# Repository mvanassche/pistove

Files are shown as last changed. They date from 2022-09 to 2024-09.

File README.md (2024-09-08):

Raspberry pi

```
sudo apt-get install openjdk-11-jdk
```
```
sudo apt-get install pigpio
```

# Hardware

## Stove

- [Manual air valve register](https://www.jpvos.be/nl/dixneuf-warmeluchtroosters-toe-afvoer/9882-register-met-kabel-diam160-met-messing-knop.html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)
- [Belimo LM230A](https://www.ventilatieland.be/fr_BE/p/belimo-servomotor-230v-o-d-5-nm-lm230a-tp/8749/) note: you can probably go with a much smaller and cheaper model
- [Air valve register](https://www.ventilatieland.be/nl_BE/p/motorbediende-regelklep-o-160mm-voor-spirobuis/8945/)

## Raspberry Pi

There are 2 versions, a cheaper version with limited display, and a more expensive with a touch screen. For both versions, a web page exposes a user interface (the same as the touch screen).  

- [ceramic oven probe, k type thermocouple](https://www.amazon.com.be/ceramic-mounting-thermocouple-sensor-temperature/dp/B09XX7Y9TY) for the hot fumes
- [MAX31855 - V2.0](https://shop.mchobby.be/fr/temperature/302-amplificateur-thermocouple-max31855-v20-3232100003026-adafruit.html)
- [Thermocouple Type-K](https://shop.mchobby.be/fr/temperature/301-thermocouple-type-k-3232100003019.html) for the cold fumes and the accumulator t°
- [SHT31-F](https://shop.mchobby.be/fr/environnemental-press-temp-hrel-gaz/1882-sht31-f-capteur-d-humidite-et-temperature-3232100018822-dfrobot.html) for indoor t°
- [Piezo buzzer](https://shop.mchobby.be/fr/autres-capteurs/57-piezo-buzzer-3232100000575.html)
- [DS18B20](https://shop.mchobby.be/fr/environnemental-press-temp-hrel-gaz/151-capteur-temperature-ds18b20-etanche-extra-3232100001510.html) for outside t°
- [Relay 5v | 2-canals](https://www.bol.com/be/nl/p/otronic-relais-module-5v-2-kanaals-arduino-esp32-esp8266-raspberry-pi-wemos/9300000011396590/) to control the register

### Version pi zero 2 W

- [Raspberry Pi Zero 2 with HEADER](https://shop.mchobby.be/fr/pi-zero-12wwh/2334-raspberry-pi-zero-2-w-avec-header-wireless-cam-port-3232100023345.html)
- [LCD 16x2 I2C](https://shop.mchobby.be/fr/afficheur-lcd-tft-oled/1807-afficheur-lcd-16x2-i2c-3232100018075-dfrobot.html)
- push buttons

### Version pi 4B

- Raspberry 4B 1G
- [4.3inch HDMI LCD (B) - 800x480 - IPS - Capacitive touch](https://www.kiwi-electronics.com/nl/4-3inch-hdmi-lcd-b-800x480-ips-capacitive-touch-4065)
- Rotary button

### Pi wiring

# Software

## Pi

`sudo nano /etc/xdg/lxsession/LXDE-pi/autostart`

```
@lxpanel --profile LXDE-pi
@pcmanfm --desktop --profile LXDE-pi
@xscreensaver -no-splash
@/etc/xdg/lxsession/LXDE-pi/stove-kiosk.sh
```

`sudo nano /etc/rc.local`

```
(cd /home/pi/stove/ && sudo java -jar pistove-2.0-SNAPSHOT-all.jar)
```

`sudo nano /etc/xdg/lxsession/LXDE-pi/stove-kiosk.sh`

```
  GNU nano 5.4                                                         /etc/xdg/lxsession/LXDE-pi/stove-kiosk.sh
#!/bin/bash

(sleep 20 && chromium-browser --kiosk http://localhost:8080/)

```

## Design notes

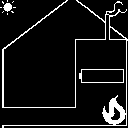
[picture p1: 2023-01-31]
src/commonMain/resources/background-oled.bmp

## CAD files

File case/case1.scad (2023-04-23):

width = 135;
height = 180;
depth = 50;

wallThickness = 2;



difference() {
    cube([height, width, depth - wallThickness]);
        // general box
    translate([-1, wallThickness, wallThickness])
        cube([height - wallThickness + 1, width - (2 * wallThickness) , depth + 1]);
        // bottom hole
    translate([30, 20, -1])
        cube([45, 80, wallThickness * 2]);
        // cable hole
    translate([150, 109 - 5, 0]) rotate([90, 0, 90])
        cylinder(h = height, r = 5);
    translate([40, 100 - 5, -1])
        cube([120, 5, 15]);

        // cover ridge
    translate([2, 2, height - 2])
        cube([height - 4, width - 4, 5]);
        // side buttons hole
    translate([16, -1, depth - 16])
        cube([54, 10, 8]);
    
        // ventilation bottom
    for (i = [0 : (width / 7)]){
        translate([height - wallThickness - 1, 10 + (i * 6), 10])
            cube([5, 3, depth - 20]);
    }    

    // hole for auto button
    translate([height - 15, 109 - 5, 33]) rotate([0, 90, 90])
        cylinder(h = height, r = 8);

    // hole for rotary button
    translate([height - 15, 109 - 5, 13]) rotate([0, 90, 90])
        cylinder(h = height, r = 4);
    
}

    // support max's
/*translate([height - 80 - 40, width - 10 - wallThickness, 22])
    cube([80, 11, wallThickness]);*/
translate([height - 80 - 40, width - 4, 0])
    cylinder(22, r = 2.5);



// cover
color("blue")
//translate([0, width + 20, 0])
rotate([180, 0, 0]) translate([0, 10, -depth])
difference() {
    cube([height + wallThickness, width, depth]);
    translate([wallThickness, -1, -1])
        cube([height + 10, width + 2, depth - wallThickness + 1]);
    
    // screen hole
    translate([14, 8, depth - wallThickness - 1])
        cube([59, 98, wallThickness * 2]);
    
        // ventilation top
    for (i = [0 : (width / 7)]){
        translate([-1, 10 + (i * 6), 10])
            cube([5, 3, depth - 20]);
    }

}

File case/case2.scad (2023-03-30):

width = 112;
height = 200;
depth = 50;

wallThickness = 2;
maxWidth = 21; // MAX81355



difference() {
    cube([height, width, depth - wallThickness]);
        // general box
    translate([-1, wallThickness, wallThickness])
        cube([height - wallThickness + 1, width - (2 * wallThickness) , depth + 1]);
    
        // bottom hole
    translate([20, 20, -1])
        cube([50, 70, wallThickness * 2]);
    
    translate([height - 50, 75, -1])
        cube([40, 16, wallThickness * 2]);
    
        // cable hole
    translate([height - 25, 20 - 5, 0]) rotate([90, 0, 0])
        cylinder(h = height, r = 5);
    translate([height - 55, 10, -1])
        cube([46, 21, 15]);

        // cover ridge
    translate([2, 2, height - 2])
        cube([height - 4, width - 4, 5]);
    
        // side buttons hole
    translate([16, -1, depth - 16])
        cube([54, 10, 8]);
    
        // ventilation bottom
    margin = 10;
    for (i = [0 : ((width - 2*margin) / 6)]){
        translate([height - wallThickness - 1, margin + (i * 6), 10])
            cube([5, 3, depth - 20]);
    }    

    // hole for auto button
    translate([height - 15, 109 - 5, 33]) rotate([0, 90, 90])
        cylinder(h = height, r = 8);

    // hole for rotary button
    translate([height - 15, 109 - 5, 13]) rotate([0, 90, 90])
        cylinder(h = height, r = 4);

    // support screen
    translate([14, (width - 99) / 2, -1]) {
        translate([0, 0, 0])
            cylinder(10, r = 1.5);
        
        translate([0, 99, 0])
            cylinder(10, r = 1.5);

        translate([60, 99, 0])
            cylinder(10, r = 1.5);

        translate([60, 0, 0])
            cylinder(10, r = 1.5);
    }
    
    // holes for screws wall
    translate([40, 10, -1])
        cylinder(10, r = 4);
    translate([36, 10, -1])
        cylinder(10, r = 2);
    translate([35, 10, -1])
        cylinder(10, r = 2);

    translate([40, width - 10, -1])
        cylinder(10, r = 4);
    translate([36, width - 10, -1])
        cylinder(10, r = 2);
    translate([35, width - 10, -1])
        cylinder(10, r = 2);
    
    // holes for max's

    for (i = [1 : 3]) {
        translate([height - (maxWidth * i)  - 50 + 7.8, width - 4, 8.5]) rotate([0, 90, 90])
            cylinder(5, r = 3.5);
    }
}

    // support max's
for (i = [1 : 3]) {
    translate([height - (maxWidth * i)  - 50, width - 4, 0])
        cylinder(5, r = 2.5);

    translate([height - (maxWidth * i) + 15  - 50, width - 4, 0])
        cylinder(5, r = 2.5);
}

    // support dispatcher
translate([14 + 60 + 10, 0, 0])
    cube([55, wallThickness + 5, wallThickness + 2]);
translate([14 + 60 + 10, wallThickness + 78 - 5, 0])
    cube([55, 5, wallThickness + 2]);


    // support screen
difference() {
    translate([14, (width - 99) / 2, 0]) {
        translate([0, 0, 0])
            cylinder(10, r = 4);
        
        translate([0, 99, 0])
            cylinder(10, r = 4);

        translate([60, 99, 0])
            cylinder(10, r = 4);

        translate([60, 0, 0])
            cylinder(10, r = 4);
    }

    translate([14, (width - 99) / 2, -1]) {
        translate([0, 0, 0])
            cylinder(10, r = 3);
        
        translate([0, 99, 0])
            cylinder(10, r = 3);

        translate([60, 99, 0])
            cylinder(10, r = 3);

        translate([60, 0, 0])
            cylinder(10, r = 3);
    }
    
}

// cover
color("blue")
    //translate([0, width + 20, 0])
    //translate([-2.2, 0 , 0])
    rotate([180, 0, 0]) translate([0, 10, -depth]) {
    difference() {
        translate([0, -0.2, 0]) cube([height + wallThickness + 1.5, width + 0.4, depth]);
        translate([wallThickness, -1, -1])
            cube([height + 10, width + 2, depth - wallThickness + 1]);
        
        // screen hole
        screenHoleWidth = 98;
        translate([14, (width - screenHoleWidth - 2*wallThickness)/2 + wallThickness, depth - wallThickness - 1])
            cube([59, screenHoleWidth, wallThickness * 2]);
        
            // ventilation top
        margin = 10;
        for (i = [0 : ((width - 2*margin) / 6)]){
            translate([-1, margin + (i * 6), 10])
                cube([5, 3, depth - 20]);
        }
        
        
    }
    // pattes
    /*translate([0, wallThickness + 0.4, depth - 5])
        cube([5, wallThickness, 5]);

    translate([0, width - wallThickness - wallThickness - 0.4, depth - 5])
        cube([5, wallThickness, 5]);*/

    /*translate([0, wallThickness + 0.5, wallThickness + 0.5])
        cube([5, wallThickness, 5]);

    translate([0, width - wallThickness - wallThickness - 0.5, wallThickness + 0.5])
        cube([5, wallThickness, 5]);*/

    translate([height - 10, wallThickness + 0.4, depth - 5])
        cube([5, wallThickness, 5]);

    translate([height - 10, width - wallThickness - wallThickness - 0.4, depth - 5])
        cube([5, wallThickness, 5]);
    
    // border
    translate([0, -wallThickness - 0.1, depth - 7])
        cube([height + wallThickness + 1.5, wallThickness, 7]);

    translate([0, -wallThickness - 0.1, 0])
        cube([15, wallThickness, depth]);


    translate([0, width + 0.1, depth - 7])
        cube([height + wallThickness + 1.5, wallThickness, 7]);
    translate([0, width + 0.1, 0])
        cube([15, wallThickness, depth]);
    
}

// stuff DO NOT PRINT
color("red") {

}

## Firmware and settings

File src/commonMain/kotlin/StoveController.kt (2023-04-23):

import kotlinx.coroutines.awaitCancellation
import kotlinx.coroutines.coroutineScope
import kotlinx.coroutines.flow.StateFlow
import kotlinx.coroutines.flow.map
import kotlinx.coroutines.flow.stateIn
import kotlinx.coroutines.launch
import kotlinx.datetime.Instant
import kotlinx.serialization.Serializable
import kotlinx.serialization.Transient
import pistove.status.physical.Environment
import kotlin.math.max
import kotlin.time.Duration.Companion.minutes
import kotlin.time.Duration.Companion.seconds


fun stoveController(): StoveController {
    val powerRelay = LowActiveGPIOElectricRelay("power-relay", 5)
    val openCloseRelay = LowActiveGPIOElectricRelay( "direction-relay", 6)
    val valve = ElectricValveController("air-intake-valve", powerRelay = powerRelay, openCloseRelay = openCloseRelay)
    //val fumes = TestTemperatureSensor("stove-thermometer").also { it.usefulPrecision = 0 }
    val fumes = MAX31855TemperaturSensor("stove-thermometer", 0, 0).also { it.usefulPrecision = 0 }
    //val accumulator = EmptyTemperatureSensor("accumulator-thermometer")
    val accumulator = MAX31855TemperaturSensor("accumulator-thermometer", 0, 1).also { it.usefulPrecision = 0 }
    val room = SHT31TemperaturSensor("room-thermometer", 1, 0x45).also { it.usefulPrecision = 1 }
    val outsideTemperatureSensor = DS18B20TempartureSensor("outside-thermometer", 0x1b9c071e64ff.toULong()).also { it.usefulPrecision = 0 }
    val buzzer = PassivePiezoBuzzerHardwarePWM("buzzer", 12)
    val openButton = PushButtonGPIO("open-button", 13, DigitalState.high)
    val closeButton = PushButtonGPIO("close-button", 26, DigitalState.high)
    val rechargeButton = PushButtonGPIO("recharge-button", 19, DigitalState.high)
    val display = Display1602LCDI2C("display", 1, 0x27)
    val comm = DisplayAndBuzzerUserCommunication("user-communication", display, buzzer)
    return StoveController("stove", valve, fumes, accumulator, room, outsideTemperatureSensor, openButton, closeButton, rechargeButton, comm)
}

@Serializable
class StoveController(
    override val id: String,
    val valve: ElectricValveController,
    val fumes: TemperatureSensor,
    val accumulator: TemperatureSensor,
    val room: TemperatureSensor,
    val outside: TemperatureSensor,
    val openButton: PushButton,
    val closeButton: PushButton,
    val rechargeButton: PushButton,
    val userCommunication: BasicUserCommunication
) : Controller {

    val accumulatorLowTemperature = 30.0
    val accumulatorHighTemperature = 130.0

    @Transient
    val lastUserValveRate = PersistentStateWithTimestamp<Double?>(null)

    @Transient
    val lastTimeRecharged = PersistentStateWithTimestamp<Unit>(Unit)

    @Transient
    var daFumes: StateFlow<InstantValue<Double>>? = null

    @Transient
    var chargedRate: StateFlow<InstantValue<Double>>? = null

    @Transient
    var autoModeController: AutoModeController? = null

    override suspend fun startControlling(): Boolean {
        // ??? what to do? should we start all here or assume they are started elsewhere?
        coroutineScope {

            val fumesSmoothed = fumes.windowed(30.0.seconds)
                .aggregate { it.average() }
                .sampleInstantValue(30.0.seconds)

            // average fumes before  deriving for less noise?
            val dFumes = fumesSmoothed.zipWithNext().map {
                if (it.second.time > it.first.time) {
                    InstantValue(
                        (it.second.value - it.first.value) / ((it.second.time.toEpochMilliseconds() - it.first.time.toEpochMilliseconds()).toDouble() / 3600000.0), // in °/h
                        Instant.fromEpochMilliseconds((it.first.time.toEpochMilliseconds() + it.second.time.toEpochMilliseconds()) / 2)
                    )
                } else {
                    InstantValue(0.0, it.second.time)
                }
            }

            launch { valve.startControlling() }
            launch { fumes.startSensing() }
            launch { accumulator.startSensing() }
            launch { room.startSensing() }
            launch { outside.startSensing() }
            launch { openButton.startSensing() }
            launch { closeButton.startSensing() }
            launch { rechargeButton.startSensing() }
            openButton.addOnClickListener { this.launch { openSome() } }
            closeButton.addOnClickListener { this.launch { closeSome() } }
            openButton.addOnLongClickListener { this.launch { open() } }
            closeButton.addOnLongClickListener { this.launch { close() } }
            rechargeButton.addOnClickListener { this.launch { onRecharged() } }
            identifieables.filterIsInstance<WatcheableState>().forEach {
                it.addOnStateChange { launch { refreshDisplay() } }
            }
            launch {
                daFumes = dFumes.windowed(5.0.minutes).map {
                    InstantValue(it.map { it.value }.average(), it.last().time)
                }.stateIn(this)
                autoModeController = SlowlyCloseWhenCooling("auto-close", valve, fumes, daFumes!!, lastUserValveRate, lastTimeRecharged)
                autoModeController?.startControlling()
            }
            launch {
                chargedRate = accumulator.windowed(5.0.minutes).map {
                    InstantValue((max(0.0, it.map { it.value }.average() - accumulatorLowTemperature) / (accumulatorHighTemperature - accumulatorLowTemperature)))
                }.stateIn(this)
            }
            awaitCancellation()
        }
        return true
    }

    override val devices: Set<Device>
        get() = setOf(fumes, accumulator, room, outside, openButton, closeButton, rechargeButton) + valve.devices + userCommunication.devices

    override val identifieables: Set<Identifiable>
        get() = devices + valve + (autoModeController?.let { setOf(it) } ?: emptySet())

    fun stopControlling() {

    }

    suspend fun setOpenRateTo(rate: Double) {
        userCommunication.acknowledge()
        lastUserValveRate.state = rate
        if(valve.setOpenRateTo(rate)) {
            userCommunication.acknowledge()
        }
    }
    suspend fun open() {
        setOpenRateTo(1.0)
    }
    suspend fun openSome() {
        setOpenRateTo((valve.openRateOrTarget ?: 0.0) + 0.1)
    }
    suspend fun closeSome() {
        setOpenRateTo((valve.openRateOrTarget ?: 1.0) - 0.1)
    }
    suspend fun close() {
        setOpenRateTo(0.0)
    }

    suspend fun auto() {
        userCommunication.acknowledge()
        autoModeController?.let { it.enabled = !it.enabled }
    }

    suspend fun onRecharged() {
        lastTimeRecharged.state = Unit
        userCommunication.acknowledge()
    }

    suspend fun refreshDisplay() {
        (userCommunication as? StringDisplay)?.displayTable(stateDisplayString())
    }
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

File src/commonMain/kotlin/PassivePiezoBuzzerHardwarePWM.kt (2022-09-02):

import kotlinx.coroutines.delay
import kotlinx.serialization.Serializable
import kotlinx.serialization.Transient
import kotlin.time.Duration

@Serializable
class PassivePiezoBuzzerHardwarePWM(override val id: String, val bcm: Int, val hardware: Boolean = (bcm in listOf(12, 13, 18, 19))) : Buzzer, TestableDevice {

    @Transient
    val pwm: GPIOPWM = pi.pwm(bcm, hardware).also {
        it.dutyCycle = 50.0
    }

    override suspend fun beep(duration: Duration) {
        beep(4000, duration)
    }

    override suspend fun beep(frequency: Int, duration: Duration) {
        pwm.frequency = frequency
        pwm.on()
        delay(duration.inWholeMilliseconds)
        pwm.off()
    }

    override suspend fun test() {
        delay(500)
        rrrrrr()
        delay(1000)
        bipBip()
        delay(500)
    }
}

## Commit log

2022-04-03 Switch to pi4j 2.1.1
    Add first lcd 1602 display
    disable the one wire temperature (to be replaced)
    [Display1602LCDI2C.kt, StoveController.kt]
2022-04-05 buttons, improve lcd, kotlin 1.6.20 official
2022-04-07 Add MAX31855
    Fix some coroutine issues
    [Display1602LCDI2C.kt, StoveController.kt]
2022-04-07 LowActive relay
    rename less confusing
2022-04-08 Device tests
2022-04-19 Switch to JS IR
2022-09-15 Add one wire support and outside thermometer
2022-10-03 continuous valve open rate
2022-10-13 serialization fix, history per month
    [Serialization.kt, Utils.kt]
2023-03-05 SPI bus
    30 mins ignition
2023-03-05 web app
    add hardware
    [case1.scad, pcb-2.fzz]
2023-04-23 rotary led toggle
    [case1.scad, pcb-2.fzz]
